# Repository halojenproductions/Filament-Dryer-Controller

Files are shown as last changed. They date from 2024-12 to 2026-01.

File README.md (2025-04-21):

# Filament Dryer Controller
## Overview
## Details
something something filament something something dry
### Processor
- ATMega328P
### Inputs
#### Button
- Pin D2
- Momentary
- Internal pull-up
#### PTC thermistor
- Pin A0
- B3950
- 100KΩ @25°C
- B-value 3950 @50°C
- 100KΩ external pull-down
#### Temperature & humudity sensor
- I2C 0x44
- SHT30-D
### Outputs
#### Ok LED
- Pin D12
- Yellow
#### Heating LED
- Pin D13
- Red
#### Display
- I2C 0x78
- 128X64 Monochrome OLED
- SH1106

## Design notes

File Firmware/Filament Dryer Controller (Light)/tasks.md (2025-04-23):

# Tasks

## Inputs
### Thermistor temp
- [x] Read
- [x] Store as degrees
- [x] Tests
### Sensor temp
- [x] Read sensor temp
- [x] Store as degrees
- [x] Tests
### Humidity
- [x] Read humidity
- [x] Store as percent
- [x] Tests
### Button 
- [x] Handle interrupt
- [ ] Tests
### Input validation
- [x] Ensure values are within acceptible range
- [x] Trigger error state
- [ ] Handle error state
- [ ] Tests

## Control loop
- [ ] Active loop
- [ ] Idle loop
- [ ] Tests
- [ ] Safety checks
- [ ] Fail safe

## Output
### Heater
- [ ] Active
- [ ] Tests
### Fan
- [ ] Active
- [ ] Idle
- [ ] Tests
### Display
- [x] Show filament details
- [x] Show realtime
- [x] Sleep timeout
- [x] Tests

## Persist config
- [x] Save on apply
- [x] Restore on startup

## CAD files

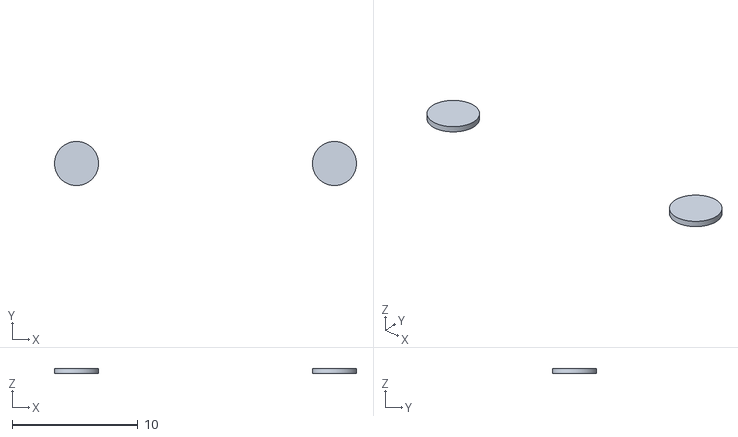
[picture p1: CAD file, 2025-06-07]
Physical/FDC_Main_Models/FDC_Panel_Front_Lenses.stl
24.0 x 3.50 x 0.402

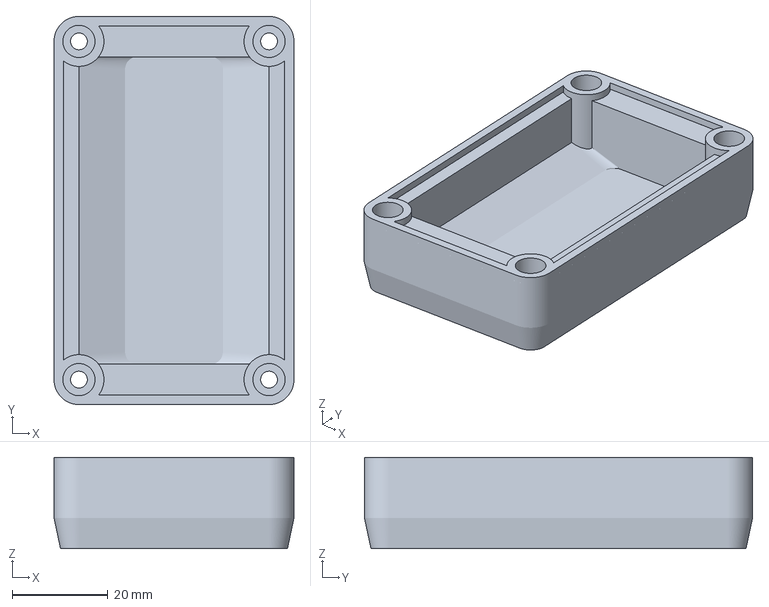
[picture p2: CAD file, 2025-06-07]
Physical/FDC_Panel_Back.3mf
50.1 x 81.0 x 19.1 mm

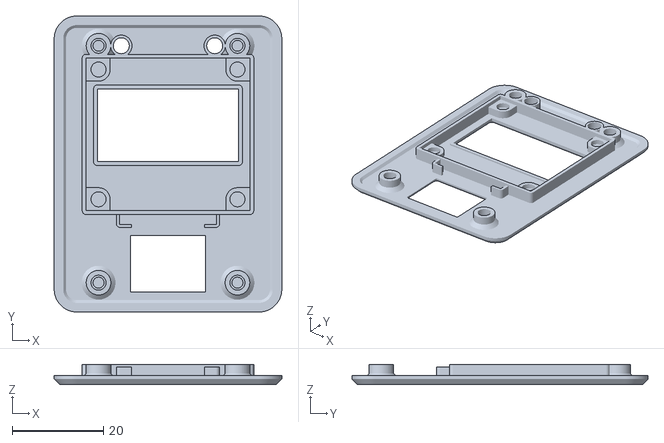
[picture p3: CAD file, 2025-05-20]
Physical/Models/FDC_Panel_Front.stl
50.0 x 65.0 x 4.40

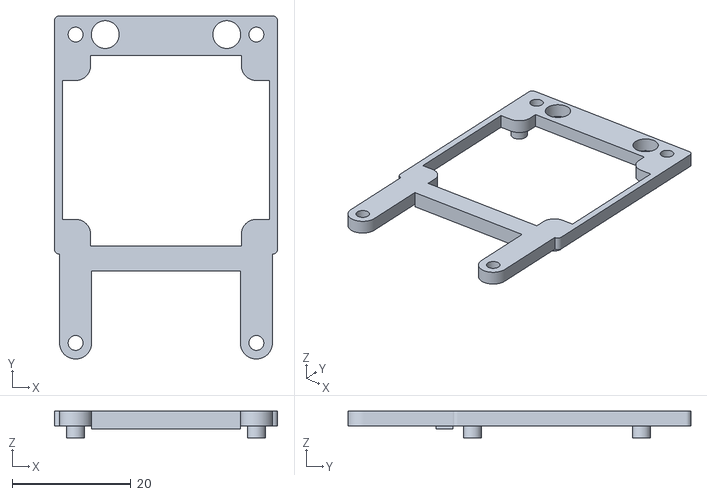
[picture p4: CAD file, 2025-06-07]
Physical/FDC_Main_Models/FDC_Panel_Frame.stl
37.7 x 57.9 x 4.50

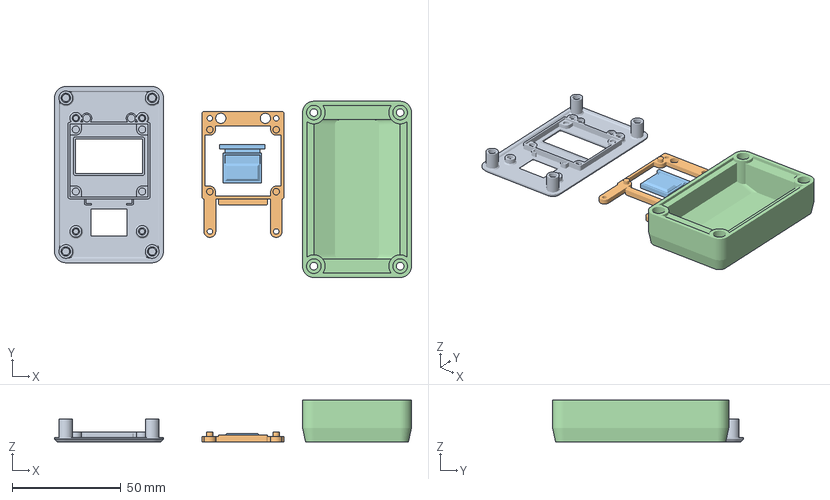
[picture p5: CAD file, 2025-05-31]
Physical/FDC_Panel.3mf
164.1 x 87.8 x 19.1 mm
FDC_Panel_Front.stl
FDC_Panel_Frame.stl
FDC_Panel_Button.stl
FDC_Panel_Back.stl

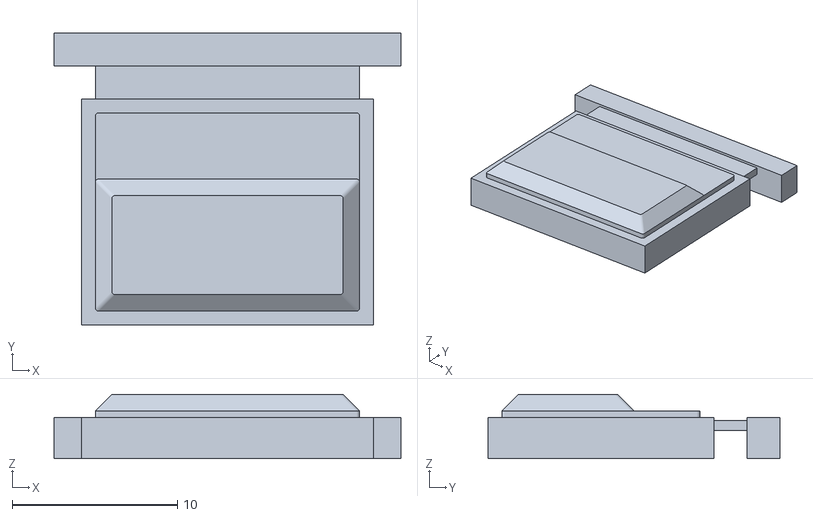
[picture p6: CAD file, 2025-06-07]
Physical/FDC_Main_Models/FDC_Panel_Button.stl
21.0 x 17.7 x 3.90

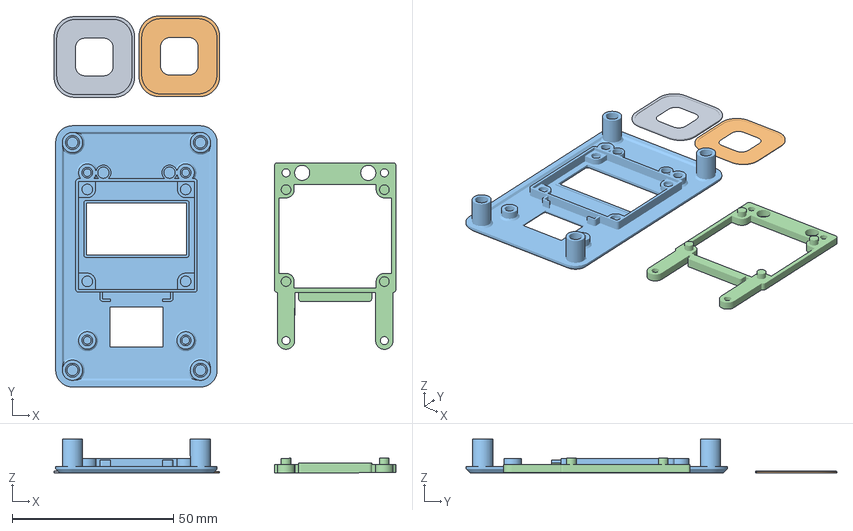
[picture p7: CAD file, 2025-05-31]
Physical/FDC_Panel_Front&Frame.3mf
106.0 x 115.0 x 10.4 mm
FDC_Panel_Front_Castle1.stl
FDC_Panel_Front_Castle2.stl
FDC_Panel_Front.stl
FDC_Panel_Frame.stl

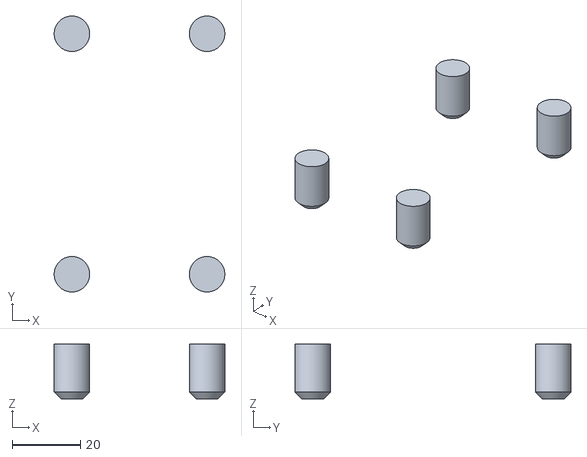
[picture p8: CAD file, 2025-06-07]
Physical/FDC_Main_Models/FDC_Panel_Back_Solid.stl
50.1 x 81.0 x 16.1

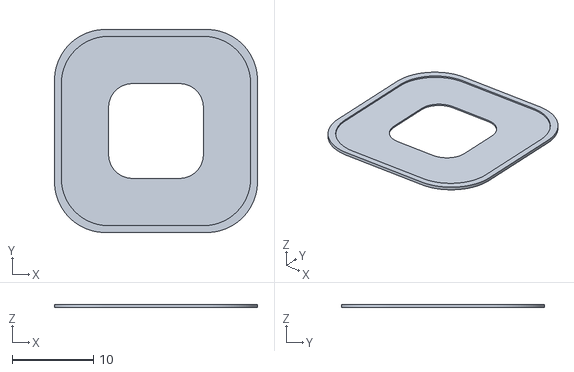
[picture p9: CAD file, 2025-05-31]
Physical/FDC_Main_Models/FDC_Panel_Front_Castle2.stl
25.0 x 25.0 x 0.4

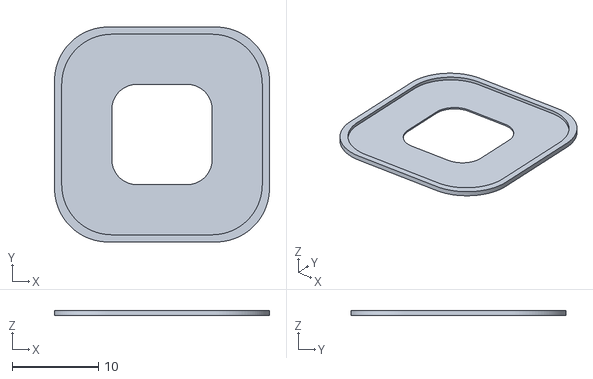
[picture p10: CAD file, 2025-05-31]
Physical/FDC_Main_Models/FDC_Panel_Front_Castle1.stl
25.0 x 25.0 x 0.6

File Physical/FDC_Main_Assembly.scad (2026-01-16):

include <FDC_Main_Shared/FDC_Main_Library.scad>
use <FDC_Main_Shared/FDC_Main_Mocks.scad>
use <FDC_Main_Base.scad>
use <FDC_Main_Top.scad>
use <FDC_Main_Intake.scad>
use <FDC_Main_Box.scad>


q = 100;
ex = [
	1, // Body top upper.
	1, // Body top lower.
	1, // Body base.
	1, // Intake.
	1, // Dessiccant box.
	1, // Dessiccant box lid.
];

/* [Hidden] */
$fn = $preview ? 50 : q;


if(ex[0]){
	// color("Tan")
	%render(10)
	BodyTop();
}

if(ex[1]){
	// color("MediumSeaGreen")
	%render(10)
	BodyTop(false);
}

if(ex[2]){
	// color("Turquoise")
	%render(10)
	BodyBase();
}

if(ex[3]){
	// color("PaleVioletRed")
	%render(10)
	Intake();
}

if(ex[4]){
	// color("PaleVioletRed")
	render(10)
	DessiccantBox();
}

if(ex[5]){
	// color("PaleVioletRed")
	render(10)
	DessiccantBoxLid();
}


// Ghosts.
%Mocks();


echo(str(
	"\n\t Dimensions ",
	"\n\t Width: ", base_dims.w,
	"\n\t Height: ", base_dims.h + top_dims.h,
	"\n\t Length: ", base_dims.l,
	"\n\t Base height: ", base_dims.h,
	"\n\t Top length: ", top_dims.l,
	"\n\t Top height: ", top_dims.h,
"\n"));

crosssections = object(
	heater_fan = PI * pow(heater_dims.fan_dia/2, 2),
	duct = duct_dims.w * duct_dims.h,
	box_bottom = box_dims.w * box_dims.l,
	channel = channel_dims.w * channel_dims.h,
	intake = intake_vent_dims.w * intake_vent_dims.h,
);

echo(str(
	"\n\t Cross sections ",
	"\n\t Heater fan: ", crosssections.heater_fan,
	"\n\t Box bottom: ", crosssections.box_bottom,
	"\n\t Duct: ", crosssections.duct,
	"\n\t Channel: ", crosssections.channel,
	"\n\t Intake: ", crosssections.intake,
"\n"));

assert(
	crosssections.heater_fan < crosssections.box_bottom, 
	"Box bottom area is too small."
);
assert(
	crosssections.heater_fan < crosssections.channel, 
	"Channel area is too small."
);
assert(
	crosssections.heater_fan < crosssections.duct, 
	"Duct area is too small."
);
assert(
	crosssections.heater_fan < crosssections.intake, 
	"Intake area is too small."
);

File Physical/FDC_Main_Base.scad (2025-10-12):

include <FDC_Main_Shared/FDC_Main_Library.scad>
use <FDC_Main_Shared/FDC_Main_Objects.scad>
use <FDC_Main_Intake.scad>

q = 100;
ex = [1,1,1,1];

/* [Hidden] */
$fn = $preview ? 50 : q;


if(ex[0]){
	BodyBase();
}

if(ex[1]){
}

module BodyBase(){
	difference(){
		union(){
			Base();
			*Seal();
		}

		Electranics_();

		Heater_();

		Channel2_();

		*trany(box_pos_y)
		Fan_();

		Intake(false);
		*Cover_();

		*TopScrews();
	}

	Clips();
	

	module Base(){
		// Main.
		ultracuber(
			[
				base_dims.w,
				base_dims.l,
				base_dims.h + base_dims.thick.b,
			],
			[
				base_dims.radii.out.b,
				[base_dims.radii.out.s, true],
				// base_dims.radii.out.t,
				parting_line_relief,
			],
			[0, 1, 1],
			[0, 0, -base_dims.thick.b],
		);
		// Top interface section.
		*ultracuber(
			[
				base_dims.w,
				top_dims.l,
				base_dims.radii.out.t,
			],
			[
				0,
				[base_dims.radii.out.s, true],
				parting_line_relief,
			],
			[0, 1, -1],
			[0, 0, base_dims.h],
		);
	}

	// Not needed when eliminating the intake section.
	module Channel2_(){
		trany(channel_pos_y){
			// Fillet.
			ultracuber(
				[
					channel_dims.w,
					channel_dims.l,
					global_dims.radii.in.t,
				],
				[
					0,
					global_dims.radii.in.s,
					0,//-global_dims.radii.in.t,
				],
				[0, 1, 1],
				[0, 0, channel_dims.h - global_dims.radii.in.t + nonzero()],
			);

			hull(){
				// 
				ultracuber(
					[
						channel_dims.w,
						channel_dims.l,
						channel_dims.h - channel_dims.slope + nonzero(),
					],
					[
						global_dims.radii.in.b,
						global_dims.radii.in.s,
						0,
					],
					[0, 1, 1],
					[0, 0, channel_dims.slope + nonzero()],
					[0, 0, 0]
				);

				// 
				ultracuber(
					[
						channel_dims.w,
						channel_dims.l - channel_dims.slope,
						channel_dims.slope,
					],
					[
						global_dims.radii.in.b,
						global_dims.radii.in.s,
						0,
					],
					[0, -1, 1],
					[0, channel_dims.l, nonzero()],
					[0, 0, 0]
				);


			}
		}
	}

	// Not needed when eliminating the intake section.
	module Channel_(){
		trany(channel_pos_y){
			// Fillet.
			ultracuber(
				[
					channel_dims.w,
					channel_dims.l,
					global_dims.radii.in.t,
				],
				[
					0,
					global_dims.radii.in.s,
					0,//-global_dims.radii.in.t,
				],
				[0, 1, 1],
				[0, 0, channel_dims.h - global_dims.radii.in.t + nonzero()],
			);

			hull(){
				// Full height, upside down.
				ultracuber(
					[
						channel_dims.w,
						channel_dims.l,
						channel_dims.h + nonzero(),
						channel_dims.w,
						channel_dims.l - channel_dims.h*2,
					],
					[
						0,
						global_dims.radii.in.s,
						global_dims.radii.in.b,
					],
					[0, -1, -1],
					[0, 0, nonzero()],
					[180, 0, 0]
				);

				// Half height, also upside down.
				ultracuber(
					[
						channel_dims.w,
						channel_dims.l/2,
						channel_dims.slope,
						channel_dims.w,
						channel_dims.l/2 - channel_dims.slope*2,
					],
					[
						0,
						global_dims.radii.in.s,
						global_dims.radii.in.b,
					],
					[0, -1, -1],
					[0, 0, nonzero()],
					[180, 0, 0]
				);


				// Big rounding at the end.
				intersection(){
					trany(channel_dims.l)
					align(
						[channel_dims.w, channel_dims.h*2, channel_dims.h*2],
						[0, -1, 1],
					)
					rotate([0, 90, 0])
					cylr(
						channel_dims.h*2, 
						channel_dims.w,
						[1, 1, 1],
						global_dims.radii.in.s[0],
						false,
					);

					ultracuber(
						[
							channel_dims.w,
							channel_dims.l,
							channel_dims.h + nonzero(),
						],
						[0, 0, 0],
						[0, 1, 1],
						[0, 0, nonzero()],
					);
				}
			}
		}
	}

	module Fan_(){
		tranz(heater_dims.fan_pos)
		align([
			heater_dims.fan_dia, 
			global_dims.divs, 
			heater_dims.fan_dia
		], [0, 1, 1])
		rotate([90, 0, 0])
		cylr(
			heater_dims.fan_dia, 
			global_dims.divs,
			[1, 1, 1],
			-.4,
			true,
		);
	}

	module Electranics_(){
		ultracuber(
			[
				electronics_dims.w,
				electronics_dims.l,
				base_dims.h + nonzero(),
			],
			[
				global_dims.radii.in.b, 
				global_dims.radii.in.s, 
				0,//-global_dims.radii.in.t
			],
			[0, 1, 1],
			[0, base_dims.thick.s, 0],
		);
	}
}

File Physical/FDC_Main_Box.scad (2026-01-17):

include <FDC_Main_Shared/FDC_Main_Library.scad>
use <FDC_Main_Shared/FDC_Main_Objects.scad>

q = 100;
ex = [
	1, // Box.
	1, // Lid.
	1, // Lid mod.
	1, // Support.
];

/* [Hidden] */
$fn = $preview ? 50 : q;


if(ex[0]){
	DessiccantBox();
}

if(ex[1]){
	DessiccantBoxLid();
}

if(ex[3]){
	DessiccantBoxSupport();
}

module DessiccantBox(){
	difference(){
		union(){
			Main();
			LidInterface();
		}

		Main_();
		Duct_();
		BottomMesh_();
		BottomSideMesh_();
		TopSideMesh_();
		BottomDoveRelief_();
	}

	module Main(){
		tranz(box_dims.pos().z - box_dims.lid().h)
		trany(box_pos_y){
			ultracuber(
				[
					box_dims.w,
					box_dims.l,
					box_dims.h - box_dims.lid().h,
				],
				[
					box_dims.thi().b,
					[box_dims.thi().s, true],
					0,
				],
				[0, 1, -1],
				[0, 0, 0],
			);
		}
	}

	module LidInterface(){
		tranz(box_dims.pos().z - box_dims.lid().h)
		trany(box_pos_y)
		intersection(){
			ultracuber(
				[
					box_dims.w,
					box_dims.l,
					box_dims.interface().h,
				],
				[
					0,
					[box_dims.thi().s, true],
					-box_dims.interface().h,
				],
				[0, 1, -1],
				[0, 0, 0],
			);

			// Intersector.
			ultracuber(
				[
					box_dims.w + box_dims.interface().h*2 - parting_line_relief*2,
					box_dims.l + box_dims.interface().h - parting_line_relief,
					box_dims.interface().h,
				],
				[0, [box_dims.thi().s + box_dims.interface().h, true], 0],
				[0, 1, -1],
				[0, 0, 0],
			);
		}
	}

	module Main_(){
		tranz(box_dims.pos().z - box_dims.lid().h)
		trany(box_pos_y){
			ultracuber(
				[
					box_dims.inner().w,
					box_dims.inner().l,
					box_dims.inner().h - box_dims.lid().h - box_dims.thi().mesh + nonzero()*2,
				],
				[
					box_dims.thi().b,
					[0, true],
					-parting_line_relief,
				],
				[0, 0, -1],
				[0, box_dims.l/2, nonzero()],
			);
		}
	}

	module Duct_(){
		// Duct.
		*trany(box_pos_y - nonzero())
		tranz(fan_low_side_pos_z)
		rotate([-90, 0, 0])
		ultracuber(
			[
				box_dims.inner().w,
				duct_dims.h,
				box_dims.inner().l + box_dims.thi().s,
			],
			[
				-parting_line_relief,
				0,
				0,
			],
			[0, 0, 1],
			[0, -nonzero(), -nonzero()],
		);
	}

	module BottomMesh_(){
		// Main.
		trany(box_pos_y)
		tranz(box_dims.pos().z - box_dims.h + box_dims.thi().b){
			ultracuber(
				[
					box_dims.inner().w,
					box_dims.inner().l + box_dims.thi().s,
					box_dims.thi().mesh + nonzero()*2,
				],
				[
					box_dims.thi().b,
					[0, true],
					0,
				],
				[0, 1, -1],
				[0, box_dims.thi().s, nonzero()],
			);
		}
	}

	module BottomSideMesh_(){
		trany(box_pos_y + box_dims.l + nonzero())
		tranz(box_dims.pos().z - box_dims.h)
		{
			ultracuber(
				[
					box_dims.inner().w,
					channel_dims.h - channel_dims.slope + box_dims.thi().b + nonzero()*2,
					box_dims.thi().mesh + nonzero()*2,
				],
				[
					box_dims.thi().b,
					[0, true],
					0,
				],
				[0, 1, 1],
				[0, 0, -nonzero()],
				[90, 0, 0],
			);

			// Corners.
			ultracuber(
				[
					box_dims.inner().w,
					box_dims.thi().b + nonzero()*2,
					box_dims.thi().b + nonzero()*2,
				],
				[
					0,
					[0, true],
					0,
				],
				[0, 1, 1],
				[0, 0, -nonzero()],
				[90, 0, 0],
			);
		}
	}

	module TopSideMesh_(){
		trany(box_pos_y + nonzero())
		tranz(fan_low_side_pos_z)
		{
			ultracuber(
				[
					box_dims.inner().w,
					duct_dims.h,
					box_dims.thi().mesh + nonzero()*2,
				],
				[
					0,
					[0, true],
					box_dims.thi().b,
				],
				[0, 0, -1],
				[0, 0, -nonzero()],
				[90, 0, 0],
			);

			// Dove relief.
			ultracuber(
				[
					box_dims.inner().w - box_dims.thi().b*2 + parting_line_relief*2,
					box_dims.thi().s + nonzero()*2,
					duct_dims.h - box_dims.thi().b*2 + parting_line_relief*2,
				],
				[
					0,
					[0, true],
					0,
				],
				[0, 1, 0],
				[0, -nonzero()*2, -nonzero()],
			);
		}
	}

	module BottomDoveRelief_(){
		trany(box_pos_y + box_dims.thi().b + box_dims.thi().s - parting_line_relief)
		tranz(box_dims.pos().z - box_dims.h)
		ultracuber(
			[
				box_dims.inner().w - box_dims.thi().b*2 + parting_line_relief*2,
				box_dims.inner().l - box_dims.thi().b + box_dims.thi().s + parting_line_relief + nonzero(),
				channel_dims.h - channel_dims.slope + parting_line_relief,
			],
			[
				0,
				[0, true],
				0,
			],
			[0, 1, 1],
			[0, 0, -nonzero()],
		);
	}
}

module DessiccantBoxSupport(){
	height = duct_dims.h - box_dims.lid().h + parting_line_relief - layers(2);

	trany(box_pos_y + nonzero())
	tranz(box_dims.pos().z - box_dims.lid().h)
	{
		ultracuber(
			[
				box_dims.inner().w - box_dims.thi().b*2 + parting_line_relief*2 - 1,
				box_dims.thi().s,
				// duct_dims.h - box_dims.thi().b*2 + parting_line_relief*2,
				height,
			],
			[
				0,
				[0, true],
				0,
			],
			[0, 1, -1],
			[0, -nonzero()*2, 0],
		);

		ultracuber(
			[
				box_dims.inner().w - box_dims.thi().b*2 + parting_line_relief*2 - 1,
				box_dims.thi().s - 1,
				// duct_dims.h - box_dims.thi().b*2 + parting_line_relief*2,
				height/2,
			],
			[
				-.5,
				[0, true],
				-.5,
			],
			[0, 1, -1],
			[0, .5-nonzero()*2, 0],
		);
	}
}

module DessiccantBoxLid(){
	difference(){
		Main();

		Main_();
		FrontChampher_();
		LidInterface_();

	}

	module Main(){
		tranz(box_dims.pos().z)
		trany(box_pos_y){
			ultracuber(
				[
					base_dims.w,
					top_dims.l - top_dims.upper_l,
					top_dims.h - top_dims.lower().h,
				],
				[
					parting_line_relief,
					[base_dims.radii.out.s, true],
					base_dims.radii.out.t,
				],
				[0, 1, -1],
				[0, 0, 0],
			);
		}
	}

	module Main_(){
		tranz(box_dims.pos().z)
		trany(box_pos_y){
			ultracuber(
				[
					hole(box_dims.w, box_dims.lid().clear),
					hole(box_dims.l, box_dims.lid().clear),
					top_dims.h - top_dims.lower().h - box_dims.lid().h,
				],
				[
					-parting_line_relief,
					0,
					0,
				],
				[0, 0, -1],
				[0, box_dims.l/2 - nonzero(), -box_dims.lid().h - nonzero()],
			);
		}

		// Duct.
		trany(box_pos_y - nonzero())
		tranz(fan_low_side_pos_z)
		rotate([-90, 0, 0])
		ultracuber(
			[
				box_dims.inner().w,
				duct_dims.h,
				box_dims.inner().l + box_dims.thi().s,
			],
			[
				-parting_line_relief,
				0,
				0,
			],
			[0, 0, 1],
			[0, -nonzero(), -nonzero()],
		);
	}

	module FrontChampher_(){
		trany(box_pos_y)
		tranz(box_dims.pos().z - box_dims.lid().h)
		ultracuber(
			[
				hole(box_dims.w, box_dims.lid().clear),
				top_dims.h - top_dims.lower().h - box_dims.lid().h,
				parting_line_relief*2,
			],
			[
				0,
				[0, true],
				-parting_line_relief,
			],
			[0, -1, -1],
			[0, 0, -nonzero()],
			[90, 0, 0],
		);

		trany(box_pos_y - nonzero())
		rotx(-90)
		hull(){
			extrude(parting_line_relief, 1)
			projection()
			rotx(90)
			LidInterface_();

			extrude(0, 1)
			offset(parting_line_relief)
			projection()
			rotx(90)
			LidInterface_();
		}
	}

	module LidInterface_(){
		tranz(box_dims.pos().z - box_dims.lid().h)
		trany(box_pos_y)
		intersection(){
			ultracuber(
				[
					hole(box_dims.w, box_dims.lid().clear),
					box_dims.l,
					box_dims.interface().h,
				],
				[
					0,
					[0, true],
					-box_dims.interface().h,
				],
				[0, 1, -1],
				[0, 0, 0],
			);
		}
	}
}

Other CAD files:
Physical/FDC_Main_Intake.scad
3D/FDC_Panel.scad
3D/FDC_Panel_Library.scad
3D/FDC_Panel_Mocks.scad
Physical/FDC_Main_Shared/FDC_Main_Library.scad
Physical/FDC_Main_Shared/FDC_Main_Mocks.scad
Physical/FDC_Main_Shared/FDC_Main_Objects.scad
Physical/FDC_Main_Top.scad
Physical/FDC_Panel.scad
Physical/FDC_Panel_Assembly.scad
Physical/FDC_Panel_Back.scad
Physical/FDC_Panel_Button.scad
Physical/FDC_Panel_Frame.scad
Physical/FDC_Panel_Front.scad
Physical/FDC_Panel_Library.scad
Physical/FDC_Panel_Mocks.scad
Physical/Models/FDC_Panel_Back.stl

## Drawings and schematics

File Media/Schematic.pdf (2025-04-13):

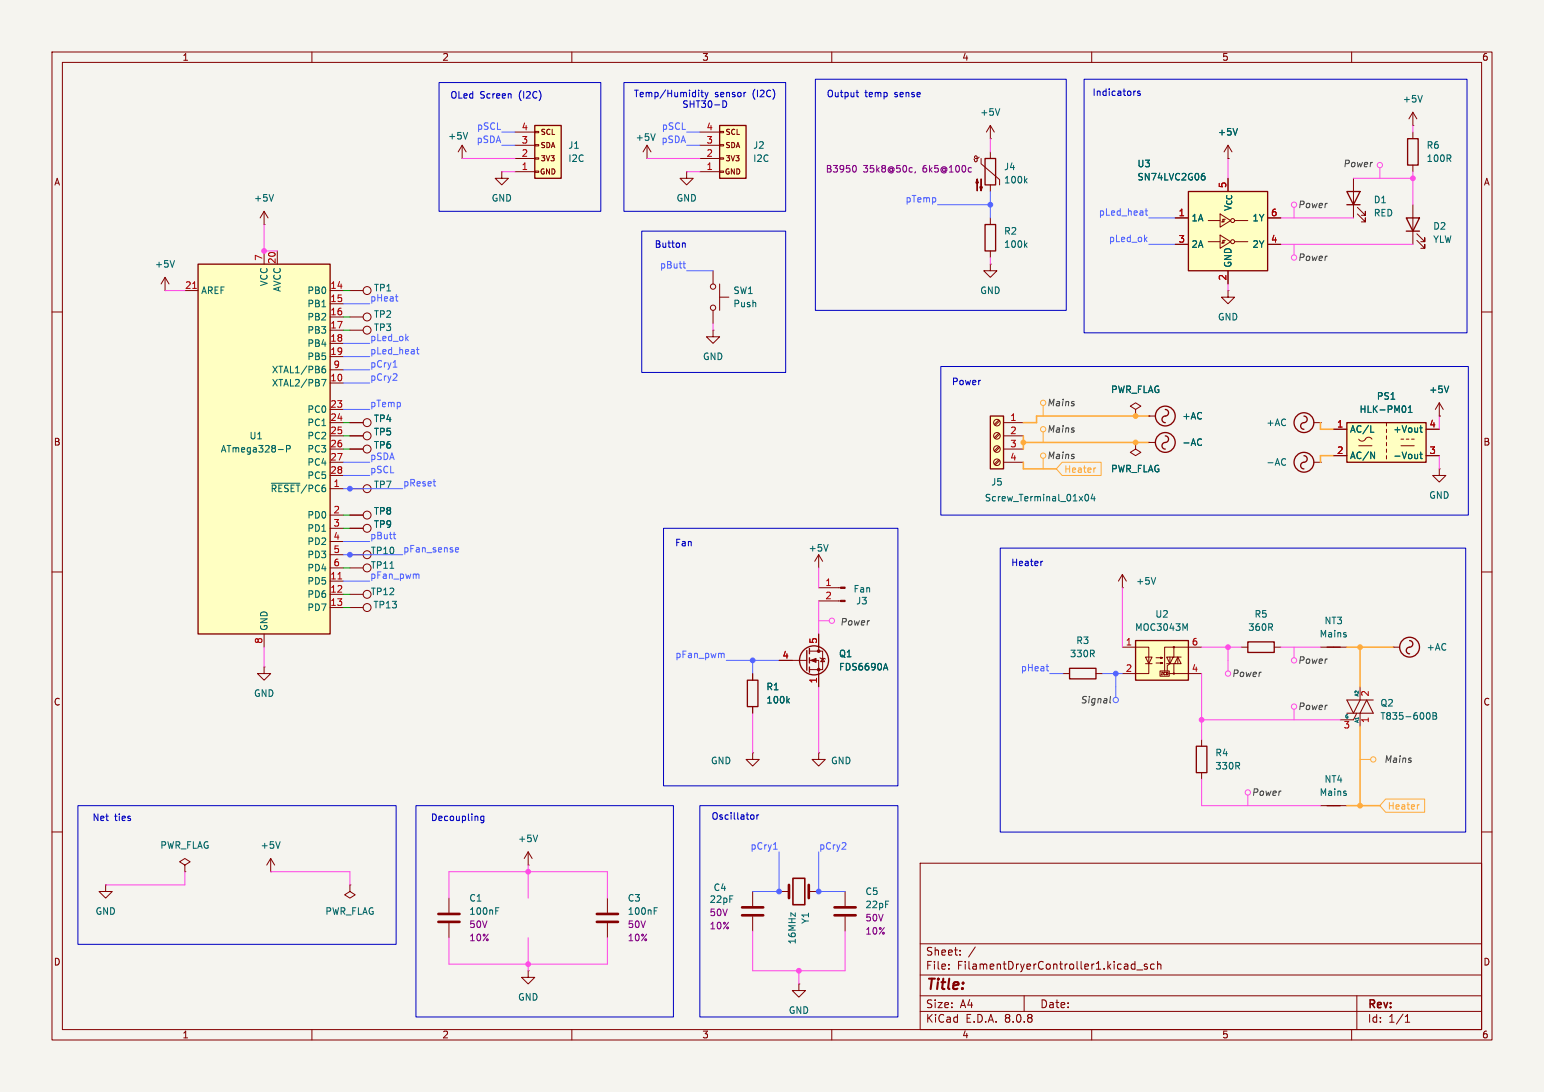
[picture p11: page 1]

Id: 1/1 Title: File: FilamentDryerController1.kicad_sch Sheet: /

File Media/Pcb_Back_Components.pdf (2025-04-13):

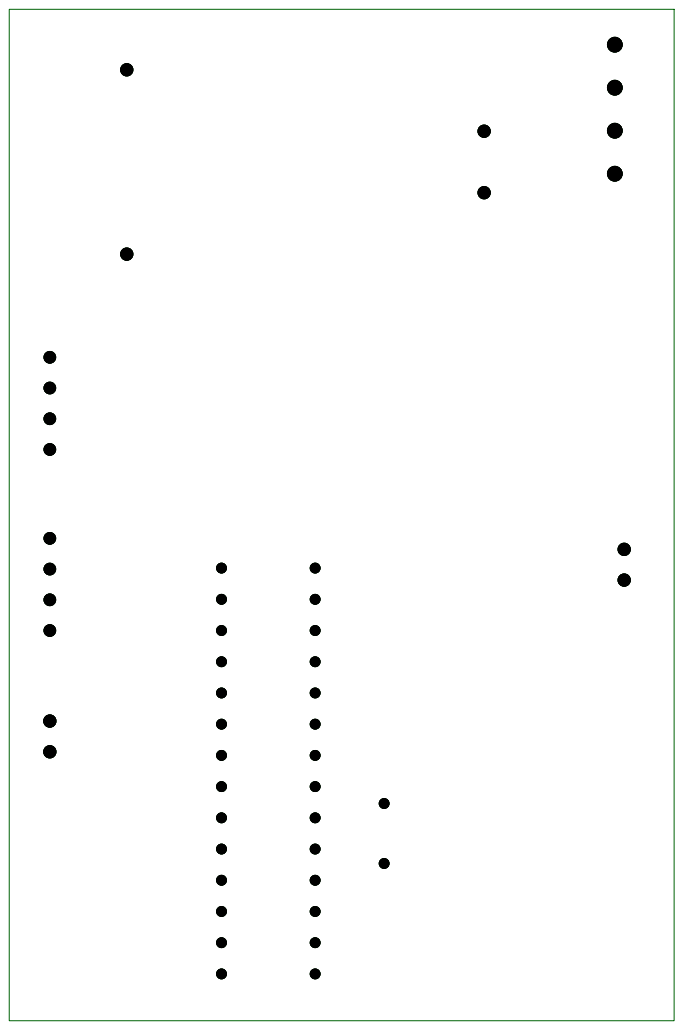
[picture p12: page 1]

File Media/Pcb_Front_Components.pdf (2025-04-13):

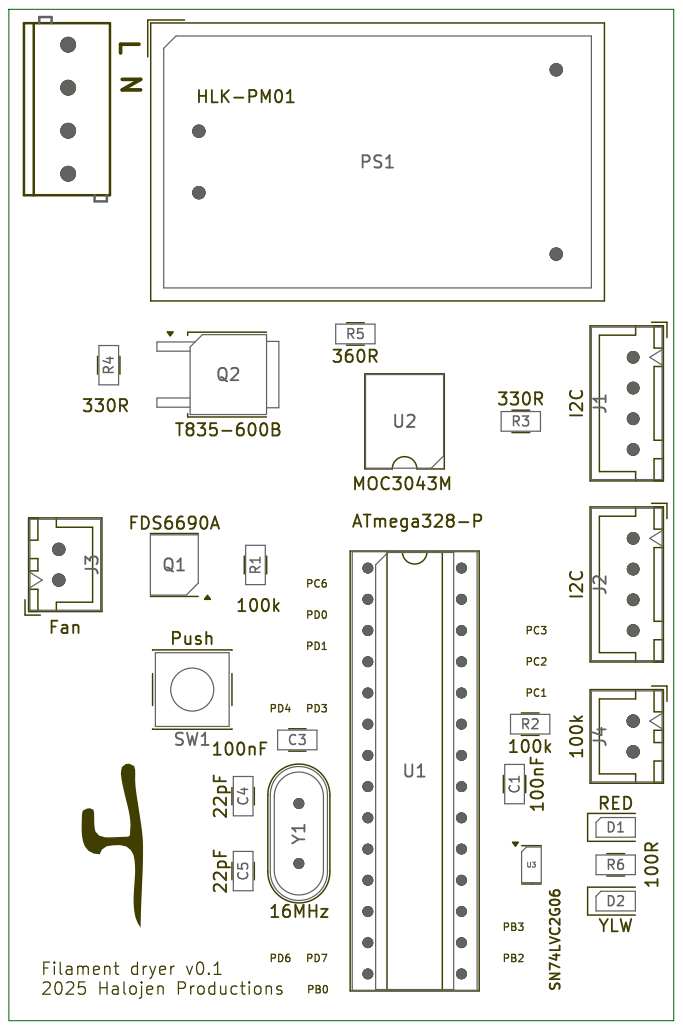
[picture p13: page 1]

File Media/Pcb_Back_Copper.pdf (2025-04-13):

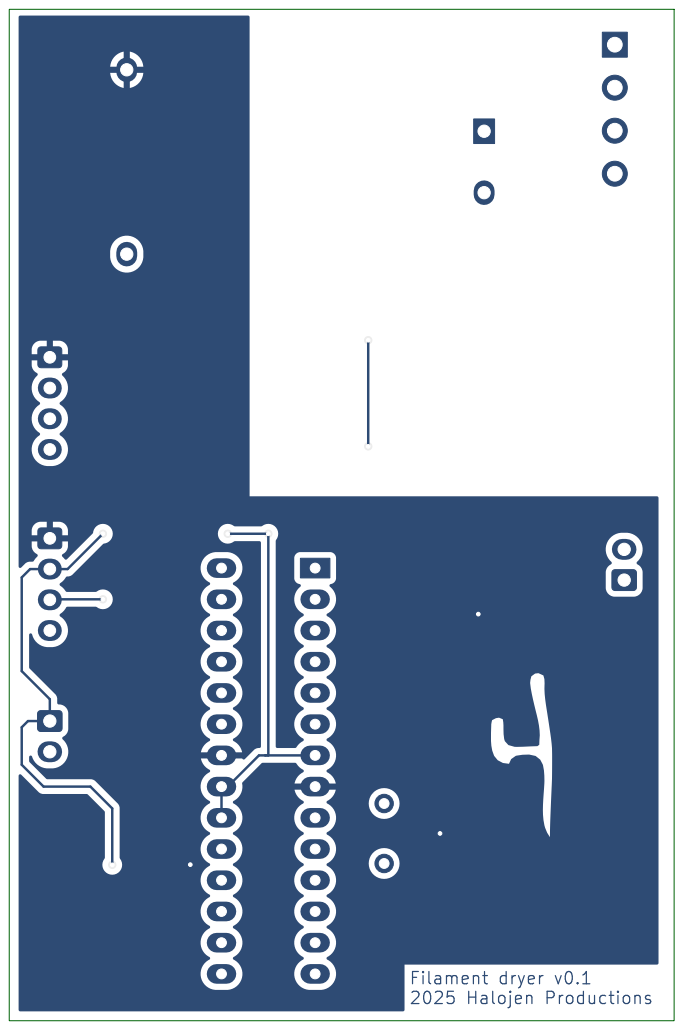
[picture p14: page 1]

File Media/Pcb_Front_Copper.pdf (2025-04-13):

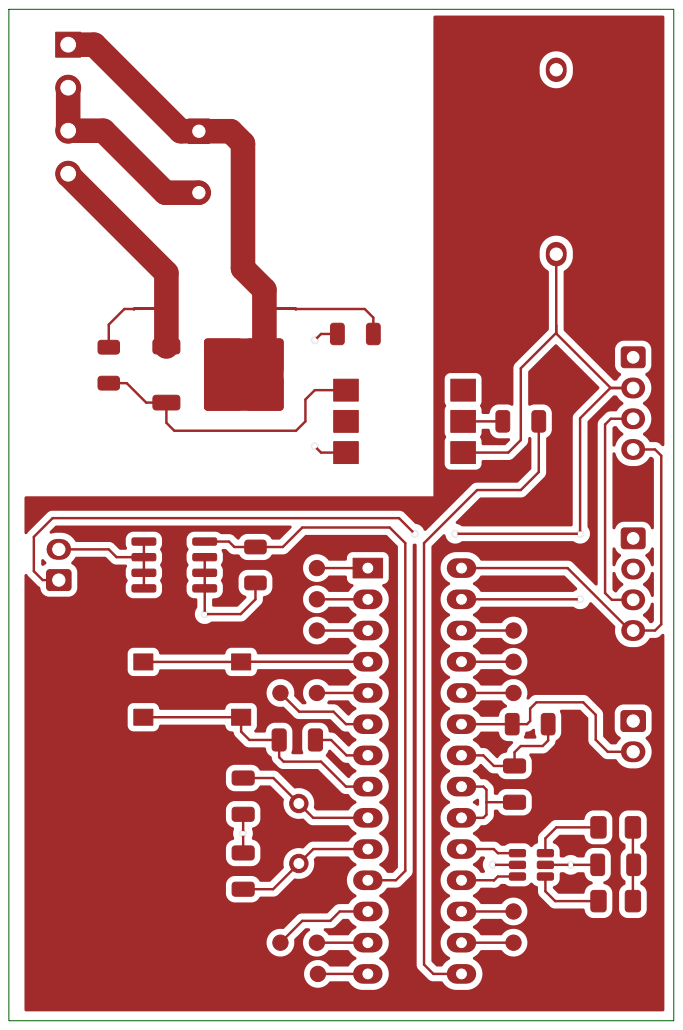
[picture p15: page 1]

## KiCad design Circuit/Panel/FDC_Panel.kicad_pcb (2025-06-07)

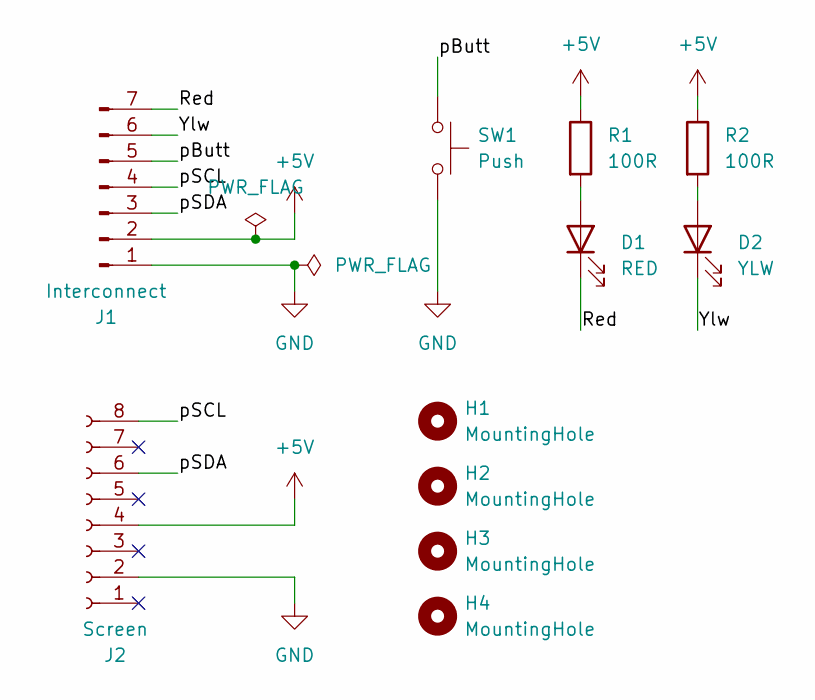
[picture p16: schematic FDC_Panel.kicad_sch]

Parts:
D1: RED; LED_D3.0mm_Clear_Flush
D2: YLW; LED_D3.0mm_Clear_Flush
H1, H2, H3, H4: MountingHole; MountingHole_2.2mm_M2
J1: Interconnect; JST_XH_S7B-XH-A_1x07_P2.50mm_Horizontal
J2: Screen; SAMTEC_HLE-104-02-F-DV-BE
R1, R2: 100R; R_1206_3216Metric
SW1: Push; Push_Button_PTS641-S-K-31

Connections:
+5V: J1.2, J2.4, R1.1, R2.1
/Red: D1.1 (K), J1.7
/Ylw: D2.1 (K), J1.6
/pButt: J1.5, SW1.2
/pSCL: J1.4, J2.8
/pSDA: J1.3, J2.6
GND: J1.1, J2.2, SW1.1
unnamed: D1.2 (A), R1.2
unnamed: D2.2 (A), R2.2

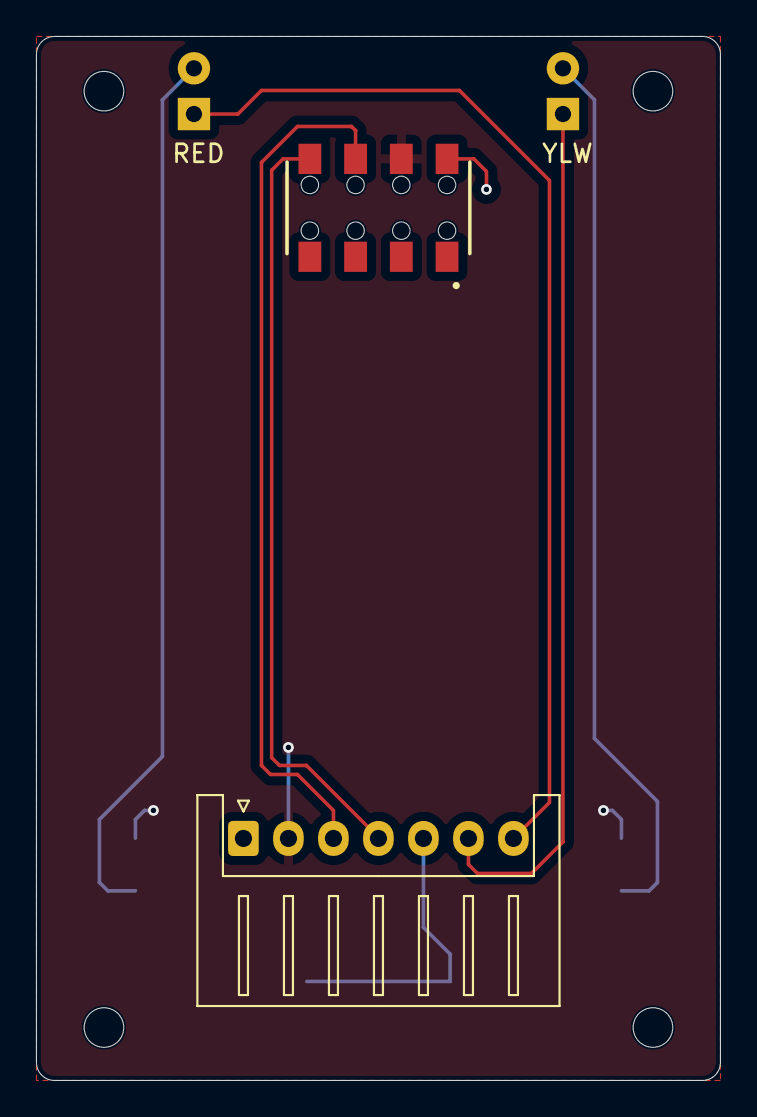
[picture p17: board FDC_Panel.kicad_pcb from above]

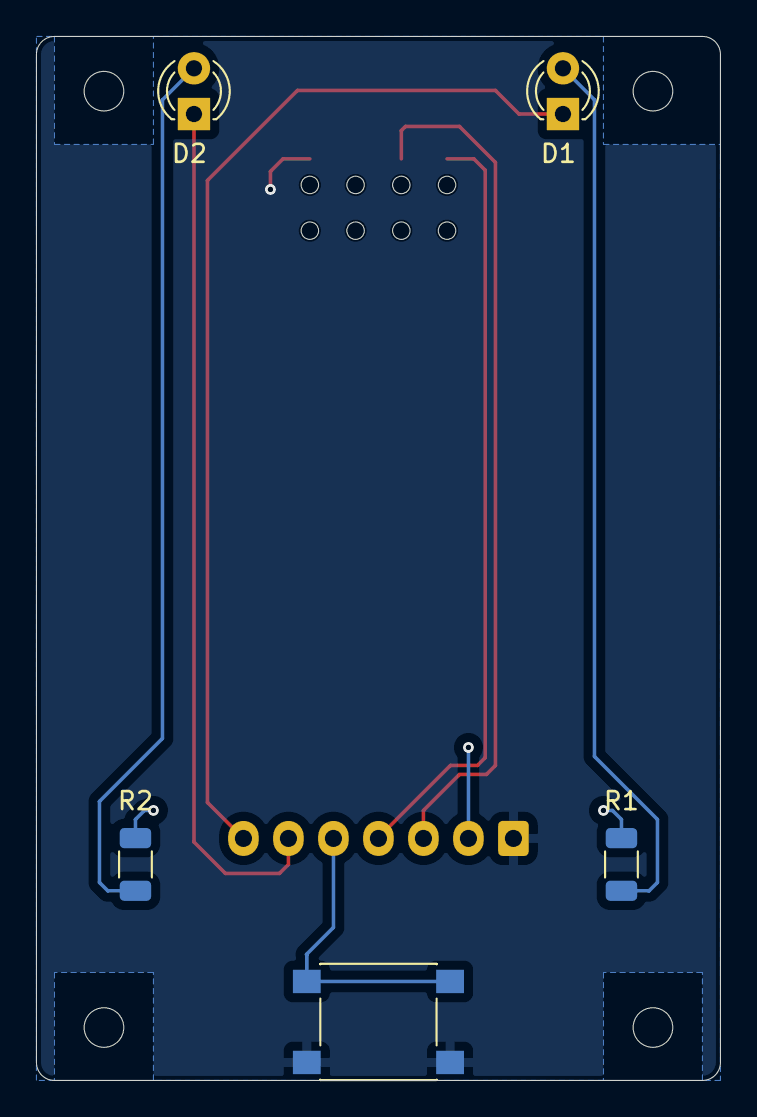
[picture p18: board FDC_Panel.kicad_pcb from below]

Board: 2 copper layers, 38.0 x 58.0 mm, 11 parts (5 on the bottom side), 9 nets.

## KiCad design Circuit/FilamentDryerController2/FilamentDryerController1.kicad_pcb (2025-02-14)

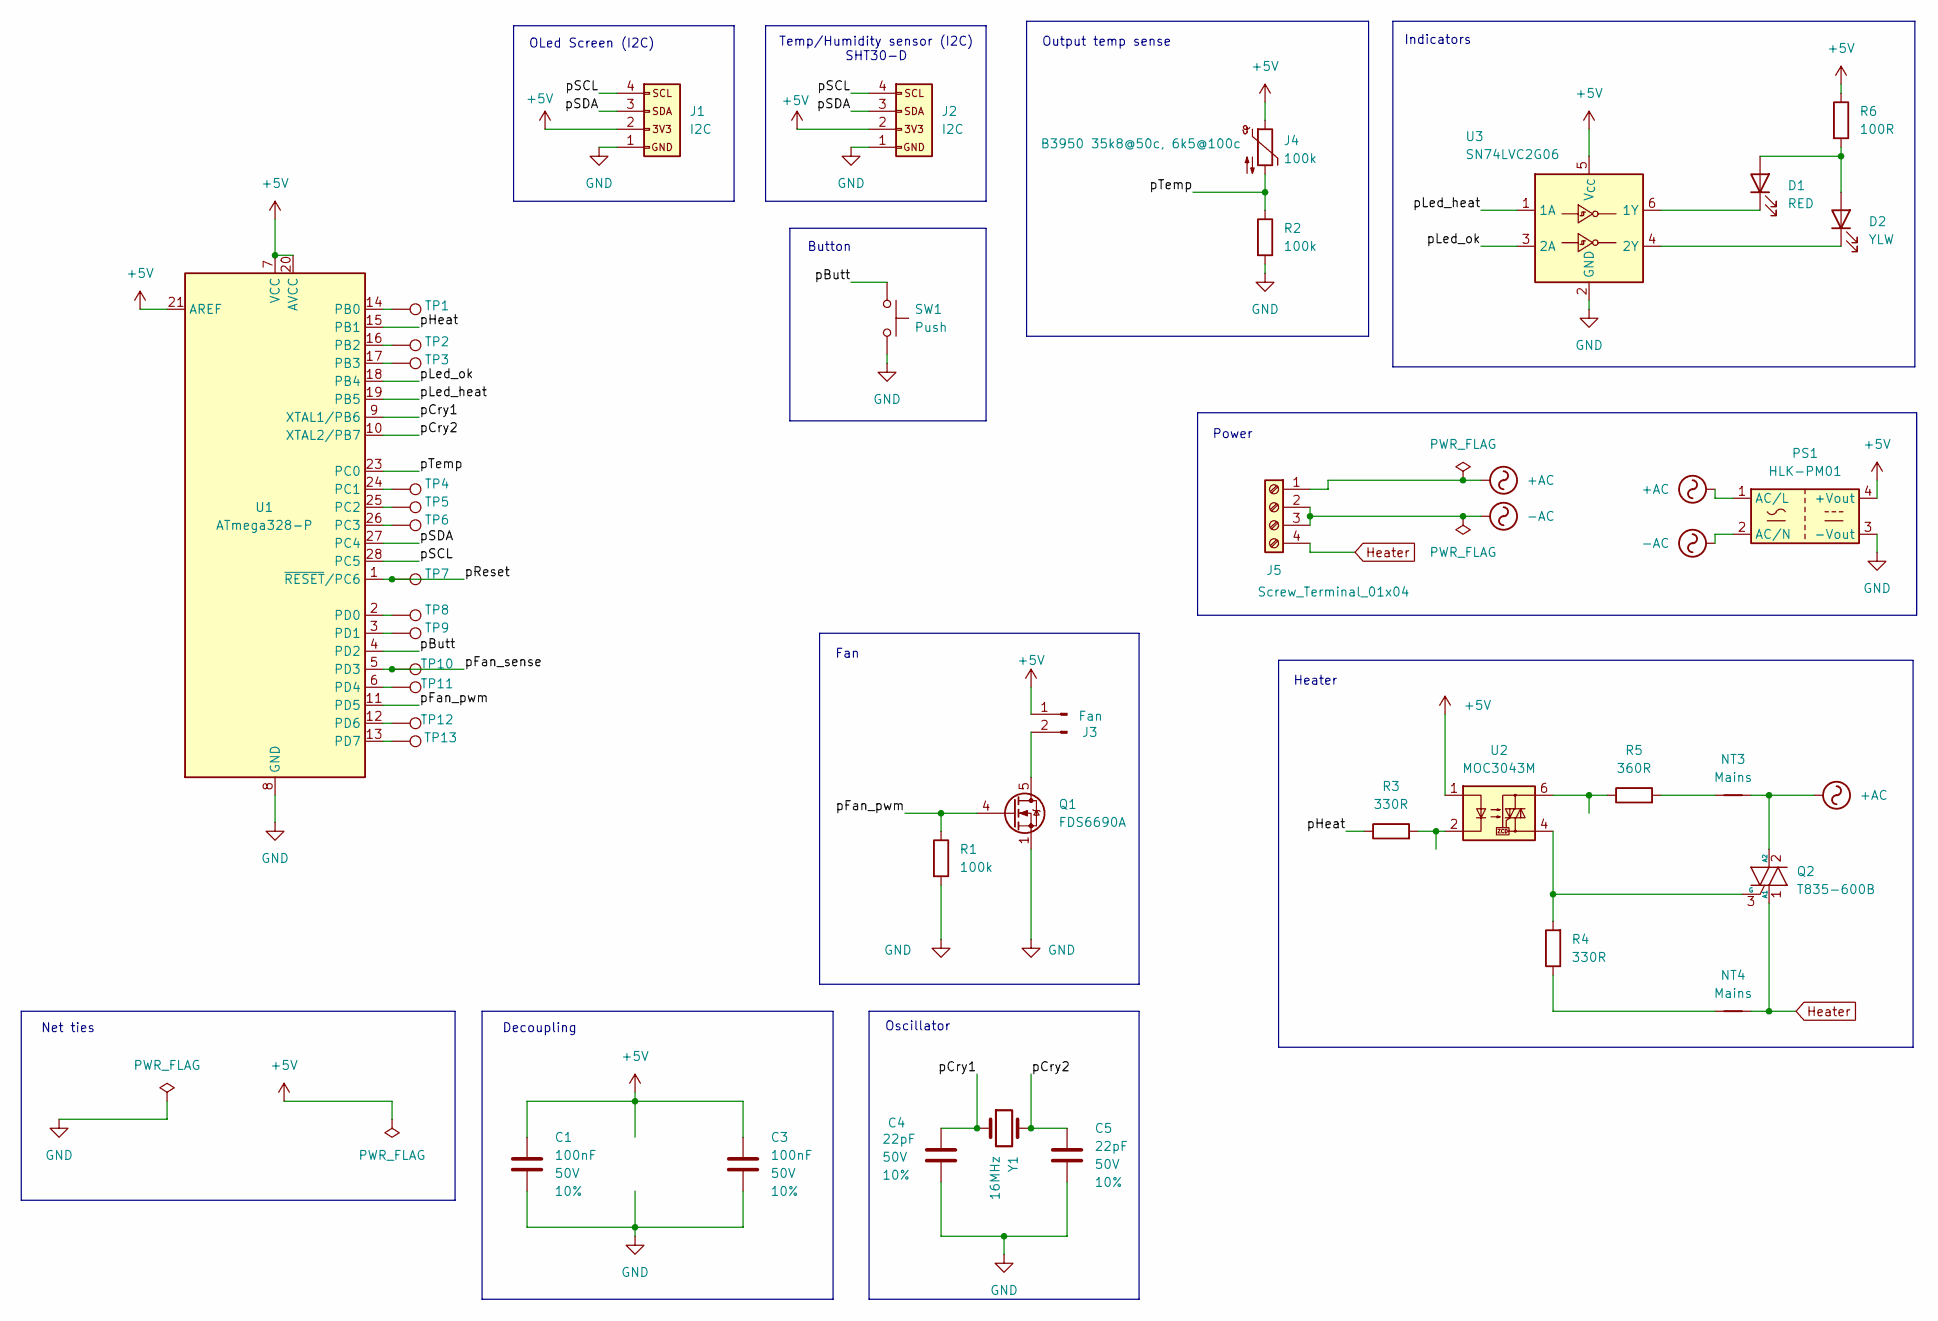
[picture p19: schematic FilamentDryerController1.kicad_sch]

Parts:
C1, C3: 100nF; C_1206_3216Metric; Voltage 50V; Tolerance 10%
C4, C5: 22pF; C_1206_3216Metric; Voltage 50V; Tolerance 10%
D1: RED; LED_1206_3216Metric
D2: YLW; LED_1206_3216Metric
J1, J2: I2C; JST_XH_B4B-XH-A_1x04_P2.50mm_Vertical
J3: Fan; JST_XH_B2B-XH-A_1x02_P2.50mm_Vertical
J4: 100k; JST_XH_B2B-XH-A_1x02_P2.50mm_Vertical
J5: Screw_Terminal_01x04; Screw_Terminal_3.5mm-4
NT3, NT4: Mains; NetTie-2_SMD_Pad0.2x2.5mm
PS1: HLK-PM01; Converter_ACDC_Hi-Link_HLK-PMxx
Q1: FDS6690A; SOIC-8_3.9x4.9mm_P1.27mm
Q2: T835-600B; TO-252-2
R1, R2: 100k; R_1206_3216Metric
R3, R4: 330R; R_1206_3216Metric
R5: 360R; R_1206_3216Metric
R6: 100R; R_1206_3216Metric
SW1: Push; SW_SPST_PTS645
TP1: PB0; TestPoint-1.25mm
TP2: PB2; TestPoint-1.25mm
TP3: PB3; TestPoint-1.25mm
TP4: PC1; TestPoint-1.25mm
TP5: PC2; TestPoint-1.25mm
TP6: PC3; TestPoint-1.25mm
TP7: PC6; TestPoint-1.25mm
TP8: PD0; TestPoint-1.25mm
TP9: PD1; TestPoint-1.25mm
TP10: PD3; TestPoint-1.25mm
TP11: PD4; TestPoint-1.25mm
TP12: PD6; TestPoint-1.25mm
TP13: PD7; TestPoint-1.25mm
U1: ATmega328-P; DIP-28_W7.62mm_Socket_LongPads
U2: MOC3043M; SMDIP-6_W9.53mm
U3: SN74LVC2G06; SOT-23-6
Y1: 16MHz; Crystal_HC49-U_Vertical

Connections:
+5V: C1.1, C3.1, J1.2, J2.2, J3.1, J4.1, PS1.4 (+Vout), R6.1, U1.7 (VCC), U1.20 (AVCC), U1.21 (AREF), U2.1, U3.5 (V_{CC})
+AC: J5.1, NT3.2, PS1.1 (AC/L), Q2.2 (A2)
-AC: J5.2, J5.3, PS1.2 (AC/N)
/pButt: SW1.2, U1.4 (PD2)
/pCry1: C4.1, U1.9 (XTAL1/PB6), Y1.1
/pCry2: C5.2, U1.10 (XTAL2/PB7), Y1.2
/pFan_pwm: Q1.4 (G), R1.1, U1.11 (PD5)
/pFan_sense: TP10.1, U1.5 (PD3)
/pHeat: R3.1, U1.15 (PB1)
/pLed_heat: U1.19 (PB5), U3.1 (1A)
/pLed_ok: U1.18 (PB4), U3.3 (2A)
/pReset: TP7.1, U1.1 (~RESET/PC6)
/pSCL: J1.4, J2.4, U1.28 (PC5)
/pSDA: J1.3, J2.3, U1.27 (PC4)
/pTemp: J4.2, R2.1, U1.23 (PC0)
GND: C1.2, C3.2, C4.2, C5.1, J1.1, J2.1, PS1.3 (-Vout), Q1.1 (S), Q1.2 (S), Q1.3 (S), R1.2, R2.2, SW1.1, U1.8 (GND), U1.22 (GND), U3.2 (GND)
Heater: J5.4, NT4.2, Q2.1 (A1)
unnamed: D1.2 (A), D2.2 (A), R6.2
unnamed: D1.1 (K), U3.6 (1Y)
unnamed: D2.1 (K), U3.4 (2Y)
unnamed: J3.2, Q1.5 (D), Q1.6 (D), Q1.7 (D), Q1.8 (D)
unnamed: NT3.1, R5.2
unnamed: NT4.1, R4.1
unnamed: Q2.3 (G), R4.2, U2.4
unnamed: R3.2, U2.2
unnamed: R5.1, U2.6
unnamed: TP1.1, U1.14 (PB0)
unnamed: TP2.1, U1.16 (PB2)
unnamed: TP3.1, U1.17 (PB3)
unnamed: TP4.1, U1.24 (PC1)
unnamed: TP5.1, U1.25 (PC2)
unnamed: TP6.1, U1.26 (PC3)
unnamed: TP8.1, U1.2 (PD0)
unnamed: TP9.1, U1.3 (PD1)
unnamed: TP11.1, U1.6 (PD4)
unnamed: TP12.1, U1.12 (PD6)
unnamed: TP13.1, U1.13 (PD7)

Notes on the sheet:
Button
Power
Fan
Net ties
OLed Screen (I2C)
Decoupling
Heater
Indicators
Oscillator
Temp/Humidity sensor (I2C) SHT30-D
Output temp sense

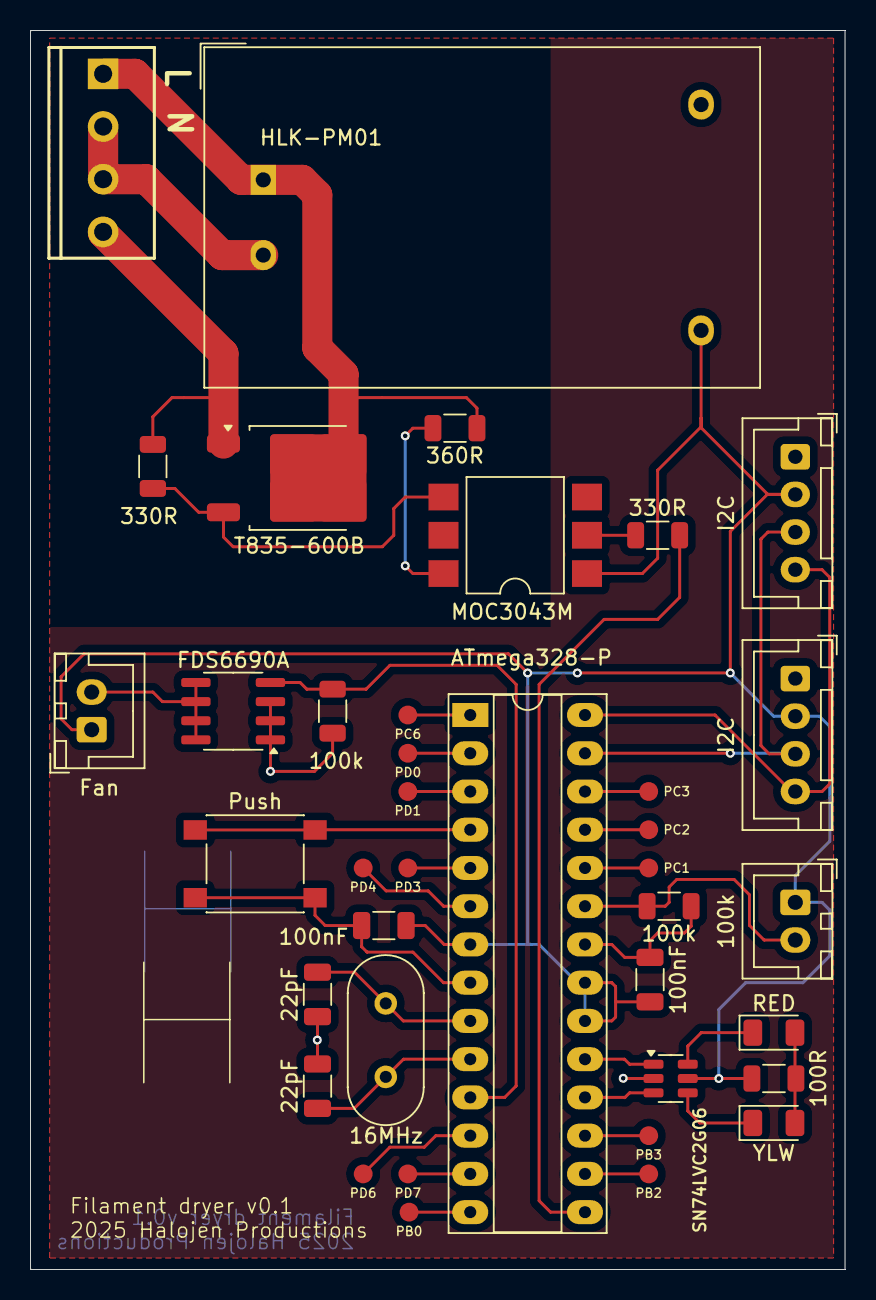
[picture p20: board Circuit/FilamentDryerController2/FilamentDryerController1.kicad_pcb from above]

Board: 2 copper layers, 54.1 x 82.3 mm, 40 parts (0 on the bottom side), 37 nets.

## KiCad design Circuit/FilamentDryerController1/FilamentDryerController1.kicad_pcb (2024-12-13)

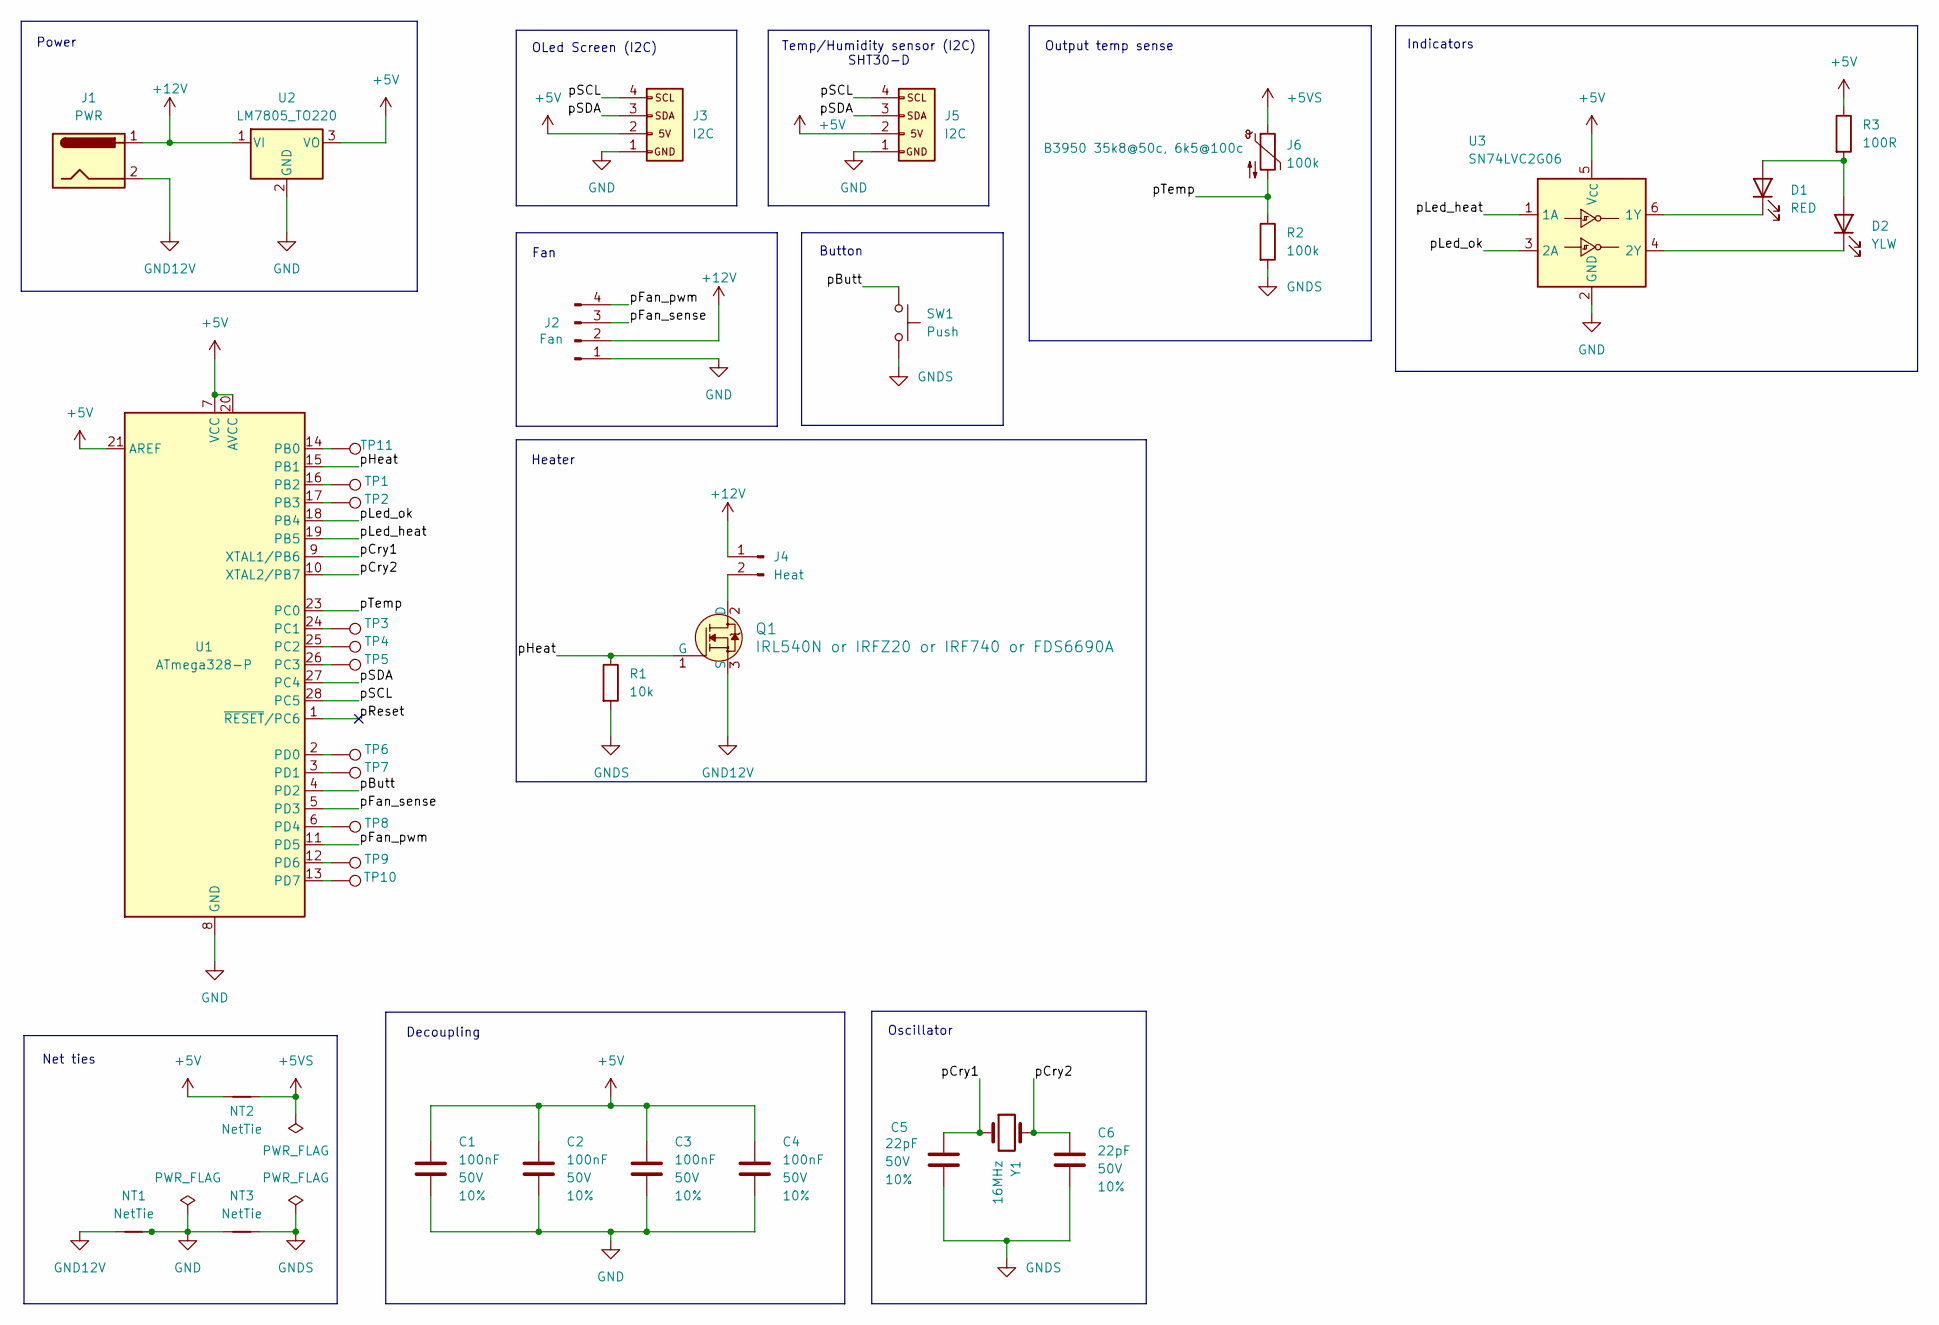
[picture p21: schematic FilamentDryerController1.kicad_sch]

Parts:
C1, C2, C3, C4: 100nF; C_1206_3216Metric; Voltage 50V; Tolerance 10%
C5, C6: 22pF; C_1206_3216Metric; Voltage 50V; Tolerance 10%
D1: RED; LED_1206_3216Metric
D2: YLW; LED_1206_3216Metric
J1: PWR; AMASS_XT30U-M_1x02_P5.0mm_Vertical
J2: Fan; JST_XH_B4B-XH-A_1x04_P2.50mm_Vertical
J3, J5: I2C; JST_XH_B4B-XH-A_1x04_P2.50mm_Vertical
J4: Heat; AMASS_XT30UPB-F_1x02_P5.0mm_Vertical
J6: 100k; JST_XH_B2B-XH-AM_1x02_P2.50mm_Vertical
NT1: NetTie; NetTie-2_SMD_Pad2.0mm
NT2, NT3: NetTie; NetTie-2_SMD_Pad0.5mm
Q1: IRL540N or IRFZ20 or IRF740 or FDS6690A; TO-220-3; MPN IRF540NPBF; Digi-Key_PN IRF540NPBF-ND
R1: 10k; R_1206_3216Metric
R2: 100k; R_1206_3216Metric
R3: 100R; R_1206_3216Metric
SW1: Push; Push_SMD_6.2x6.2mm
TP1, TP11: PB2; 1x01
TP2: PB3; 1x01
TP3: PC1; 1x01
TP4: PC2; 1x01
TP5: PC3; 1x01
TP6: PD0; 1x01
TP7: PD1; 1x01
TP8: PD4; 1x01
TP9: PD6; 1x01
TP10: PD7; 1x01
U1: ATmega328-P; DIP-28_W7.62mm_Socket_LongPads
U2: LM7805_TO220; TO-220-3_Vertical
U3: SN74LVC2G06; SOT-23-6
Y1: 16MHz; Crystal_HC49-U_Vertical

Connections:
+5V: C1.1, C2.1, C3.1, C4.1, J3.2, J5.2, NT2.1, R3.1, U1.7 (VCC), U1.20 (AVCC), U1.21 (AREF), U2.3 (VO), U3.5 (V_{CC})
+5VS: J6.1, NT2.2
+12V: J1.1, J2.2, J4.1, U2.1 (VI)
/pButt: SW1.2, U1.4 (PD2)
/pCry1: C5.1, U1.9 (XTAL1/PB6), Y1.1
/pCry2: C6.2, U1.10 (XTAL2/PB7), Y1.2
/pFan_pwm: J2.4, U1.11 (PD5)
/pFan_sense: J2.3, U1.5 (PD3)
/pHeat: Q1.1 (G), R1.1, U1.15 (PB1)
/pLed_heat: U1.19 (PB5), U3.1 (1A)
/pLed_ok: U1.18 (PB4), U3.3 (2A)
/pReset: U1.1 (~RESET/PC6)
/pSCL: J3.4, J5.4, U1.28 (PC5)
/pSDA: J3.3, J5.3, U1.27 (PC4)
/pTemp: J6.2, R2.1, U1.23 (PC0)
GND: C1.2, C2.2, C3.2, C4.2, J2.1, J3.1, J5.1, NT1.2, NT3.1, U1.8 (GND), U1.22 (GND), U2.2 (GND), U3.2 (GND)
GND12V: J1.2, NT1.1, Q1.3 (S)
GNDS: C5.2, C6.1, NT3.2, R1.2, R2.2, SW1.1
unnamed: D1.2 (A), D2.2 (A), R3.2
unnamed: D1.1 (K), U3.6 (1Y)
unnamed: D2.1 (K), U3.4 (2Y)
unnamed: J4.2, Q1.2 (D)
unnamed: TP11.1, U1.14 (PB0)
unnamed: TP1.1, U1.16 (PB2)
unnamed: TP2.1, U1.17 (PB3)
unnamed: TP3.1, U1.24 (PC1)
unnamed: TP4.1, U1.25 (PC2)
unnamed: TP5.1, U1.26 (PC3)
unnamed: TP6.1, U1.2 (PD0)
unnamed: TP7.1, U1.3 (PD1)
unnamed: TP8.1, U1.6 (PD4)
unnamed: TP9.1, U1.12 (PD6)
unnamed: TP10.1, U1.13 (PD7)

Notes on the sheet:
Button
Power
Fan
Net ties
OLed Screen (I2C)
Decoupling
Heater
Indicators
Oscillator
Temp/Humidity sensor (I2C) SHT30-D
Output temp sense

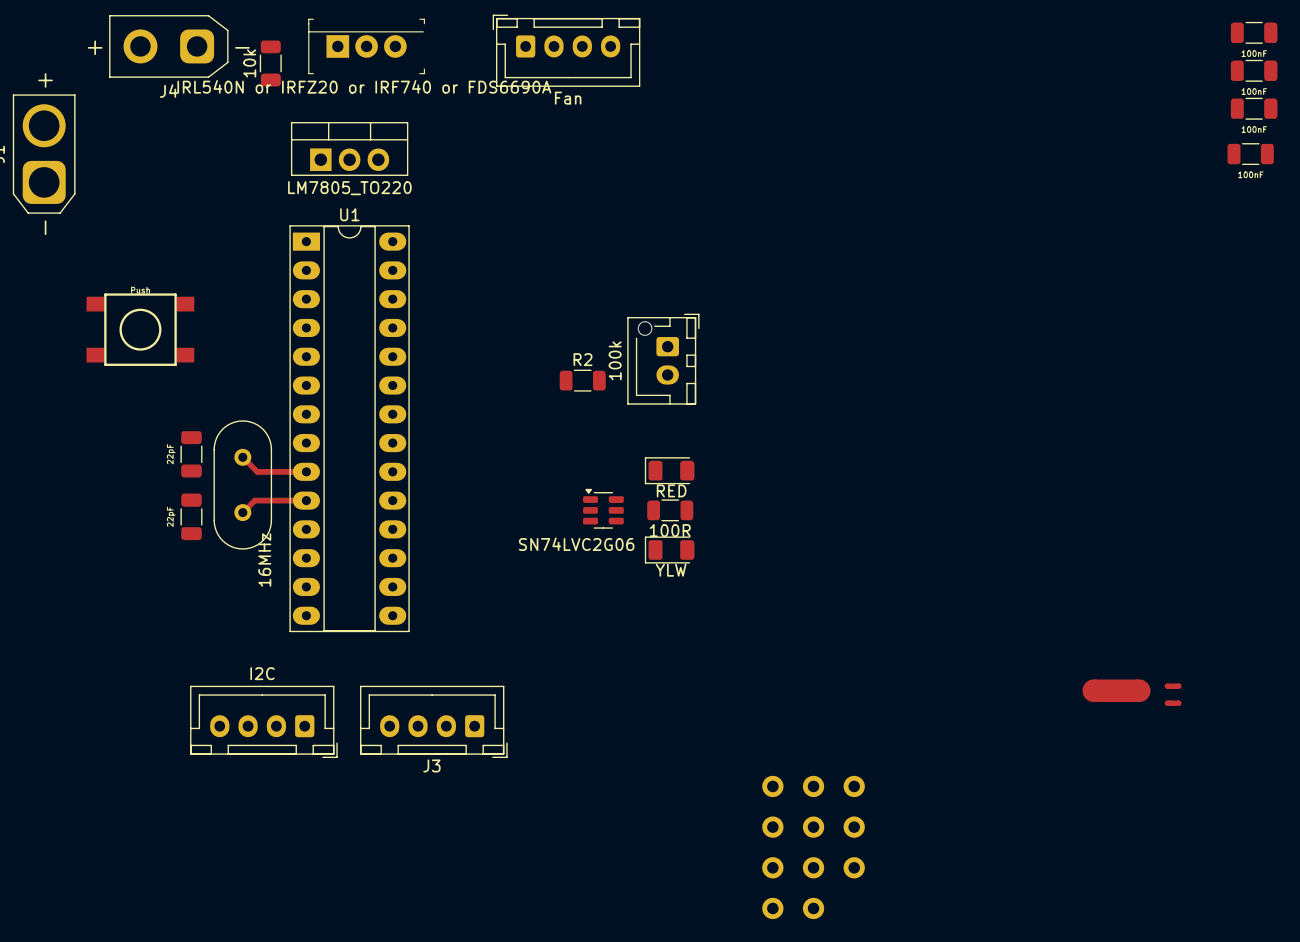
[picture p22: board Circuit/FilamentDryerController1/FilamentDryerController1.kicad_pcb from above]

Board: 2 copper layers, 37 parts (0 on the bottom side), 32 nets.

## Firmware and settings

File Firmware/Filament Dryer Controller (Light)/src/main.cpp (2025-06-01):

// #include <Adafruit_GFX.h>
#include <Arduino.h>
// #include <u8g2lib.h>

#include "button.h"
#include "control.h"
#include "filaments.h"
#include "htsensor.h"
#include "pins.h"
#include "system.h"
#include "ui.h"
#include "utilities.h"

#define DEBUG_MODE 0

void setup() {
	// Setup serial write output.
	delay(1000);

	Serial.begin(9600);
	while (!Serial) {	 // Wait for serial port to connect
		delay(10);
	}
	Serial.println(F(""));
	Serial.println(F("> Setup start"));

	// Set up pins.
	// Serial.println(F("Pins"));
	Serial.println(F("Pins::setupPins()"));
	Pins::setupPins();

	// Load saved filament.
	Serial.println(F("Filaments::retrieve()"));
	Filaments::retrieve();

	// Set up oled display.
	// Serial.println("UI");
	Serial.println(F("UI::setupScreen()"));
	UI::setupScreen();

	// ops.currentTime = millis();

	// TODO move to a setup method in HtSensor.
	// Set up humidity & temperature sensor.
	Serial.println(F("HtSensor::setupSensor()"));
	HtSensor::setupSensor();

	// Set up button interrupt.
	Serial.println(F("Attaching interrupt"));
	attachInterrupt(digitalPinToInterrupt(Pins::pButt), Button::interruptHandler, CHANGE);

	// Set initial values.
	Serial.println(F("Setting initial values"));
	Util::clearCommand(Sys::Command::HandleButtonHold);
	Util::setCommand(Sys::Command::WakeUp);
	digitalWrite(Pins::pLedOk, LOW);
	Util::setStatus(Sys::Status::Active);
	// Control::idle();

	// Serial.println(F("Setup finished"));
}

void loop() {
	// Serial.println(F(""));
	// Serial.println(F("> Main loop start"));

	Sys::currentTime = millis();

	// Wrangle interruption.
	if (Button::interrupted()) {
		// Button changed state. Go and deal with that.
		Button::interruptAnalyser();
	}

	// Wake up.
	if (Util::checkCommand(Sys::Command::WakeUp)) {
		UI::wakeUp();
	}

	if (Util::getStatus(Sys::Status::ButtonDown)) {
		// Touch timers.
		Util::resetTimer(Sys::screenTimeout);
		Util::resetTimer(Sys::selectionTimeout);
	}

	// Button held.
	if (Util::getStatus(Sys::Status::ButtonDown)
		&& Util::getTimer(Sys::buttonHoldTimeout)
		&& Util::getCommand(Sys::Command::HandleButtonHold)) {
		Button::buttonHeld();
	}

	// Read sensors.

	if ((Util::getStatus(Sys::Status::Active) && Util::checkTimer(Sys::activeInputPolling))
		|| (!Util::getStatus(Sys::Status::Active) && Util::checkTimer(Sys::idleInputPolling))) {
		// Serial.println(F("Read sensors"));

		/// Check thermistor.
		// TODO Remove mocky shit.
		Util::checkTherm(50);
		// TODO uncomment: ops.checkTherm(Thermistor::adcToCelsius(analogRead(Pins::pTemp)));

		/// Check humidity.
		// TODO Remove mocky shit.
		// float humidity = 50 + (int)random(2);
		// if (Util::checkHumidity(humidity)) {
		if (Util::checkHumidity(HtSensor::sensor.readHumidity())) {
			UI::setDirty(UI::Dirty::Humidity);
		}

		/// Check temperature.
		// TODO Remove mocky shit.
		// float inTemperature = 20 + (int)random(2);
		// if (Util::checkTemperature(inTemperature)) {
		if (Util::checkTemperature(HtSensor::sensor.readTemperature())) {
			UI::setDirty(UI::Dirty::Temp);
		}
	}

	if (Sys::sensHumid > Filaments::activeFilament.humidity) {
		Util::setStatus(Sys::Status::Moist);
	} else {
		Util::clearStatus(Sys::Status::Moist);
	}

	// Control loop.
	if (Util::getStatus(Sys::Status::Active)) {
		Control::active();
	} else {
		Control::idle();
	}

	// Set ok led. I'm tempted to rename it to status led.
	if (!Util::hasError()) {
		digitalWrite(Pins::pLedOk, HIGH);
	} else {
		// TODO: flash for warnings.
		digitalWrite(Pins::pLedOk, LOW);
	}

	if (Util::getStatus(Sys::Status::Heating)) {
	}

	// Update display.
	if (Util::getStatus(Sys::Status::ScreenAwake)) {
		/* Only for full frame buffer.
		// Load the display buffer.
		UI::drawUI();

		// Send the display buffer (or just bits of it).
		UI::updateScreen_FullFrameBuffer();
		*/

		UI::updateScreen();

		// Selection timeout.
		if (Util::getStatus(Sys::Status::Select) && Util::checkTimer(Sys::selectionTimeout)) {
			Serial.println(F("Selection timeout"));
			Util::clearStatus(Sys::Status::Select);
			Filaments::cancel();
			UI::setDirty(UI::Dirty::Filament);
		}

		// Screen timeout.
		if (!Util::getStatus(Sys::Status::ButtonDown) && Util::checkTimer(Sys::screenTimeout)) {
			Serial.println(F("Screen timeout."));
			UI::sleep();
		}
	}
}

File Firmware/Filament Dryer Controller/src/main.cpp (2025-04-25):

#include <Adafruit_GFX.h>
#include <Arduino.h>
#include <u8g2lib.h>

#include "button.h"
#include "controlLoop.h"
#include "filaments.h"
#include "ht.h"
#include "operations.h"
#include "pins.h"
#include "ui.h"

#define DEBUG_MODE 0

Ops& ops			 = Ops::getInstance();
Filaments& filaments = Filaments::getInstance();

int freeRam() {
	extern int __heap_start, *__brkval;
	int v;
	return (int)&v - (__brkval == 0 ? (int)&__heap_start : (int)__brkval);
}

void printMemoryUsage() {
	Serial.println(F("Memory Usage:"));

	Serial.print(F("Ops singleton: "));
	Serial.println(sizeof(Ops));

	Serial.print(F("Filaments singleton: "));
	Serial.println(sizeof(Filaments));

	Serial.print(F("UI screen: "));
	Serial.println(sizeof(U8G2_SH1106_128X64_NONAME_F_HW_I2C));

	Serial.print(F("HT sensor: "));
	Serial.println(sizeof(Adafruit_SHT31));
}

void setup() {
	// Setup serial write output.
	delay(1000);

	// Set up pins.
	// Serial.println(F("Pins"));
	Pins::setupPins();

	Serial.begin(9600);
	while (!Serial) {	 // Wait for serial port to connect
		delay(10);
	}
	Serial.println(F("Setup start"));

	Serial.print(F("Free RAM before display init: "));
	Serial.println(freeRam());
	printMemoryUsage();

	// Set up oled display.
	// Serial.println("UI");
	UI::setupScreen();
	Serial.println(F("UI setup complete"));

	Serial.print(F("Free RAM after display init: "));
	Serial.println(freeRam());
	printMemoryUsage();

	ops.currentTime = millis();

	// TODO move to a setup method in HT.
	// Set up humidity & temperature sensor.
	if (!HT::sensor.begin(0x44)) {
		// TODO Uncomment when sensor is connected.
		// ops.setStatus(Ops::Status::Error);	  // TODO handle error.
	}
	Serial.println(F("Sensor setup complete"));

	// Set up button interrupt.
	attachInterrupt(digitalPinToInterrupt(Pins::pButt), Button::interruptHandler, CHANGE);
	Serial.println(F("Interrupt attached"));

	// Set initial values.
	ops.setCommand(Ops::Command::ButtonHoldHandled);
	ops.setCommand(Ops::Command::WakeUp);
	ops.setStatus(Ops::Status::Ok);
	digitalWrite(Pins::pLedOk, ops.getStatus(Ops::Status::Ok) ? HIGH : LOW);
	ops.setStatus(Ops::Status::Active);
	Serial.println(F("Initial values set"));
	// ControlLoop::idle();

	// Serial.println(F("Setup finished"));
}

void loop() {
	Serial.println(F("Main loop start"));

	ops.currentTime = millis();
	Serial.println(F("currentTime set"));

	// Wrangle interruption.
	if (Button::interrupted()) {
		Serial.println(F("interruptAnalyser"));
		// Button changed state. Go and deal with that.
		Button::interruptAnalyser();
	}
	// Wake up.
	if (ops.checkCommand(Ops::Command::WakeUp)) {
		Serial.println(F("Command::WakeUp"));
		UI::wakeUp();
		Serial.println(F("Finished WakeUp"));
	}

	// Button held.
	if (ops.getStatus(Ops::Status::ButtonDown)
		// && ops.buttonHold.get(ops.currentTime)
		&& ops.getTimer(Ops::Timers::ButtonHold)
		&& !ops.getCommand(Ops::Command::ButtonHoldHandled)) {
		Serial.println(F("buttonHeld"));
		Button::buttonHeld();
	}

	// Button clicked.
	if (ops.checkCommand(Ops::Command::ButtonClicked)) {
		Serial.println(F("buttonClicked"));
		Button::buttonClicked();
	} else {
		// TODO remove this delay.
		Serial.println(F("Button not clicked"));
	}

	// Read sensors.
	
	if ((ops.getStatus(Ops::Status::Active)
		 // && ops.inputPollingActive.check(ops.currentTime)
		 && ops.checkTimer(Ops::Timers::InputPollingActive))
		|| (!ops.getStatus(Ops::Status::Active)
			// && ops.inputPollingIdle.check(ops.currentTime)
			&& ops.checkTimer(Ops::Timers::InputPollingIdle))) {
		Serial.println(F("Read sensors"));

		/// Check thermistor.
		// TODO Remove mocky shit.
		ops.checkTherm(50);
		// ops.checkTherm(Thermistor::adcToCelsius(analogRead(Pins::pTemp)));

		/// Check humidity.
		// TODO Remove mocky shit.
		float humidity = 50 + (int)random(2);
		if (ops.checkHumidity(humidity)) {
			// if(ops.checkHumidity(HT::sensor.readHumidity())) {
			ops.setDirty(Ops::Dirty::Humidity);
		}

		/// Check temperature.
		// TODO Remove mocky shit.
		float inTemperature = 20 + (int)random(2);
		if (ops.checkTemperature(inTemperature)) {
			// if(ops.checkTemperature(HT::sensor.readTemperature())) {
			ops.setDirty(Ops::Dirty::Temp);
		}
	}
	

	delay(5000);	// TODO remove this delay.
	// return;
	// Control loop.
	/*
	if (ops.getStatus(Ops::Status::Active)) {
		Serial.println(F("active"));
		ControlLoop::active();
	} else {
		Serial.println(F("idle"));
		// ControlLoop::idle();
	}
	*/

	// Set statuses. or should that be commands?
	if (ops.getStatus(Ops::Status::Error)) {
		Serial.println(F("Status::Error"));

		ops.clearStatus(Ops::Status::Ok);
		digitalWrite(Pins::pLedOk, ops.getStatus(Ops::Status::Ok) ? HIGH : LOW);
	}

	if (ops.getStatus(Ops::Status::Heating)) {
	}

	// Update display.
	if (ops.getStatus(Ops::Status::ScreenAwake)) {
		// Load the display buffer.
#if DEBUG_MODE
		UI::drawAreaBorders();			  // Draw the area borders
		ops.setDirty(Ops::Dirty::All);	  // Mark all areas as dirty
#endif
		Serial.println(F("drawAll"));
		UI::drawAll();

		// Send the display buffer (or just bits of it).
		Serial.println(F("updateScreen"));
		UI::updateScreen();

		// Selection timeout.
		if (ops.getStatus(Ops::Status::Select)
			// && ops.selectionTimeout.check(ops.currentTime)
			&& ops.checkTimer(Ops::Timers::SelectionTimeout)) {
			Serial.println(F("Selection timeout"));
			ops.clearStatus(Ops::Status::Select);
			filaments.cancel();
			ops.setDirty(Ops::Dirty::Filament);
		}

		// Screen timeout.
		if (!ops.getStatus(Ops::Status::ButtonDown)
			// && ops.screenTimeout.check(ops.currentTime)
			&& ops.checkTimer(Ops::Timers::ScreenTimeout)) {
			Serial.println(F("Screen timeout."));
			UI::sleep();
		}
	}
}

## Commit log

2025-01-03 Changed heat to AC. Still need to figure out fan.
    [FilamentDryerController1.kicad_sch]
2025-01-04 Pcb done.
    [FilamentDryerController1.kicad_pcb, FilamentDryerController1.kicad_sch]
2025-01-18 First pcb prototype fabricated.
    [FilamentDryerController1.kicad_pcb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]
2025-02-01 Better bom.
2025-02-14 PCB fabricated.
    [FilamentDryerController1.kicad_pcb, FilamentDryerController1.kicad_sch]
2025-04-18 Ops, commands, temps (wrong)
    [main.cpp]
2025-04-19 Timer class.
2025-04-19 Timer tests.
2025-04-19 Interrupt done. And some user interaction.
2025-04-19 Weird bugs. I'll have to use methods for getting filaments.
    [main.cpp]
2025-04-21 Renamed temperature to thermistor. Started hum/temp sensor.
2025-04-21 Simplified Thermistor. Added sensor checks.
2025-04-23 Sensor temp tests.
2025-04-23 Fixed millis bug i just introduced when moving currentTime to Ops.
    [main.cpp]
2025-04-25 Completely broken. Not enough RAM.
    I'm going to start again.
    [main.cpp]
2025-04-25 Stripped down, but buggy.
    And only slightly smaller than before so i wasted my time.
    [main.cpp, test_Conversion.cpp]
2025-04-26 Button hold bug fixed. Partial frame buffer.
    Yeah.. rewriting the whole thing only saved about 1% or RAM and still ran out. So now we have shitty code AND shitty screen refresh. I did so much improvement on the button logic that I don't want to go back now.
    [main.cpp]
2025-04-29 Panel storted.
    [FDC_Panel.scad, FDC_Panel.stl, FDC_Panel_Library.scad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]
2025-04-30 Retention frame started.
    [FDC_Panel.3mf, FDC_Panel.scad, FDC_Panel.stl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]
2025-05-02 Frame now with holes.
    [FDC_Panel.scad, FDC_Panel_Frame.scad, FDC_Panel_Library.scad]
2025-05-02 Screen shroud. Separated export models.
    [FDC_Panel.3mf, FDC_Panel.scad, FDC_Panel.stl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]
2025-05-03 Screws through both pcbs. Not going to work.
    [FDC_Panel.3mf, FDC_Panel.scad, FDC_Panel_Frame.scad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]
2025-05-04 Frame screws back to the outside.
    [FDC_Panel.3mf, FDC_Panel.scad, FDC_Panel_Frame.scad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]
2025-05-13 Button added.
    [FDC_Panel.3mf, FDC_Panel.scad, FDC_Panel_Button.scad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]
2025-05-13 Changed to assembly approach.
    [FDC_Panel_Assembly.scad, FDC_Panel_Button.scad, FDC_Panel_Button.stl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]
2025-05-13 Ditched the annoying screen viewport -2 thing.
    [FDC_Panel_Frame.scad, FDC_Panel_Front.scad, FDC_Panel_Library.scad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]
2025-05-14 Button looking good.
    [FDC_Panel_Button.scad, FDC_Panel_Button.stl, FDC_Panel_Frame.stl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]
2025-05-17 Button redesign.
    [FDC_Panel.3mf, FDC_Panel_Button.scad, FDC_Panel_Frame.scad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]
2025-05-17 Tiny button tweak.
    [FDC_Panel_Button.scad]
2025-05-18 Pcb screw posts + some tweaks.
    [FDC_Panel_Assembly.scad, FDC_Panel_Front.scad, FDC_Panel_Library.scad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]
2025-05-20 Frame redesign.
    [FDC_Panel.3mf, FDC_Panel_Assembly.scad, FDC_Panel_Button.stl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]
2025-05-20 Button redesign again.
    [FDC_Panel.3mf, FDC_Panel_Button.scad, FDC_Panel_Button.stl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]
2025-05-24 Added the back.
    [FDC_Panel.3mf, FDC_Panel_Assembly.scad, FDC_Panel_Back.scad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]
2025-05-31 Lenses added. Back tweaked for printability.
    [FDC_Panel.3mf, FDC_Panel_Assembly.scad, FDC_Panel_Back.scad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]
2025-05-31 Added test to prove timer check will handle millis() overflow.
2025-05-31 Added some filament profiles.
2025-06-07 Panel PCB, rendered mock, low profile header.
    [FDC_Main.kicad_pcb, FDC_Main.kicad_sch, FDC_Panel.kicad_pcb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]
2025-06-07 Button anchor full width.
    [FDC_Panel_Assembly.scad, FDC_Panel_Frame.scad]
2025-06-07 Panel PCB almost done.
    [FDC_Panel.kicad_pcb, FDC_Panel.kicad_sch, FDC_Panel_Assembly.scad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]
2025-09-21 Nested projects.
    [FDC_Main.kicad_sch, FDC_Panel.kicad_sch]
2025-09-21 Main started.
    [FDC_Main_Assembly.scad, FDC_Main_Base.scad, FDC_Main_Library.scad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]
2025-09-23 Slight redesign.
    [FDC_Main_Assembly.scad, FDC_Main_Base.scad, FDC_Main_Library.scad]
2025-09-28 Added a fan teardrop hole.
    [FDC_Main_Base.scad]
2025-09-28 Trying to decide where to put the sensor.
    [FDC_Main_Assembly.scad, FDC_Main_Base.scad, FDC_Main_Library.scad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]
2025-10-03 I think i finally figured out the heater position.
    [FDC_Main_Assembly.scad, FDC_Main_Base.scad, FDC_Main_Library.scad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]
2025-10-03 Electronics cavity.
    [FDC_Main_Base.scad, FDC_Main_Library.scad]
2025-10-03 Rearranged files. Separated top from base.
    [FDC_Main_Assembly.scad, FDC_Main_Base.scad, FDC_Main_Box.scad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]
2025-10-04 Cover started, interface mostly done.
    [FDC_Main_Assembly.scad, FDC_Main_Base.scad, FDC_Main_Cover.scad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]
2025-10-05 Top screws & shrouds.
    [FDC_Main_Assembly.scad, FDC_Main_Base.scad, FDC_Main_Library.scad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]
2025-10-05 Started redesigning.
    [FDC_Main_Base.scad, FDC_Main_Library.scad, FDC_Main_Mocks.scad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]
2025-10-11 More new positions sorted.
    [FDC_Main_Assembly.scad, FDC_Main_Base.scad, FDC_Main_Library.scad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]
2025-10-11 Working on interface.
    [FDC_Main_Assembly.scad, FDC_Main_Base.scad, FDC_Main_Library.scad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]
2025-10-12 Base interface & clips largely done.
    [FDC_Main_Base.scad, FDC_Main_Library.scad, FDC_Main_Objects.scad]
2025-10-12 Interface pretty much done.
    [FDC_Main_Base.scad, FDC_Main_Library.scad, FDC_Main_Objects.scad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]
2025-10-12 Eliminated the intake section.
    [FDC_Main_Assembly.scad, FDC_Main_Base.scad, FDC_Main_Library.scad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]
2025-10-12 Intake panel started.
    [FDC_Main_Assembly.scad, FDC_Main_Base.scad, FDC_Main_Cover.scad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]
2025-10-12 Intake positive done.
    [FDC_Main_Base.scad, FDC_Main_Intake.scad, FDC_Main_Library.scad]
2025-10-13 Intake negative done.
    [FDC_Main_Assembly.scad, FDC_Main_Intake.scad]
2026-01-16 Started desiccant box. KiCad 9.
    [FDC_Main_Assembly.scad, FDC_Main_Box.scad, FDC_Main_Library.scad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]
2026-01-16 More desiccant box progress.
    [FDC_Main_Assembly.scad, FDC_Main_Box.scad, FDC_Main_Library.scad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]
2026-01-16 More box progress.
    [FDC_Main_Box.scad]
2026-01-16 Added support that's needed because i'm a dumass.
    [FDC_Main_Box.scad, FDC_Main_Library.scad]
2026-01-17 Makercoin started.
    [FDC_Main_Box.scad, FDC_Main_Library.scad]
